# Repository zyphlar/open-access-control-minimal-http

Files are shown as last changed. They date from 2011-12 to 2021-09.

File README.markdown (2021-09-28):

Open Access Control - HTTP Minimal Edition
======================================
AKA Open Access Control Interlock
---------------------------------

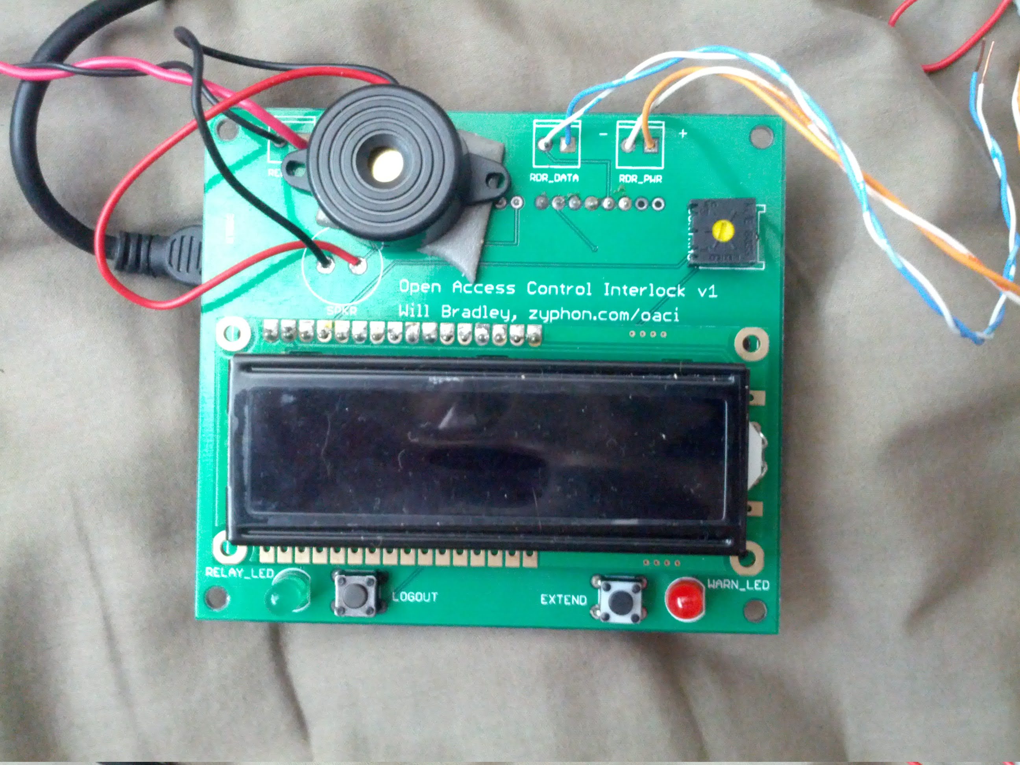
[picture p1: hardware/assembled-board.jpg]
Photo of interlock circuit board
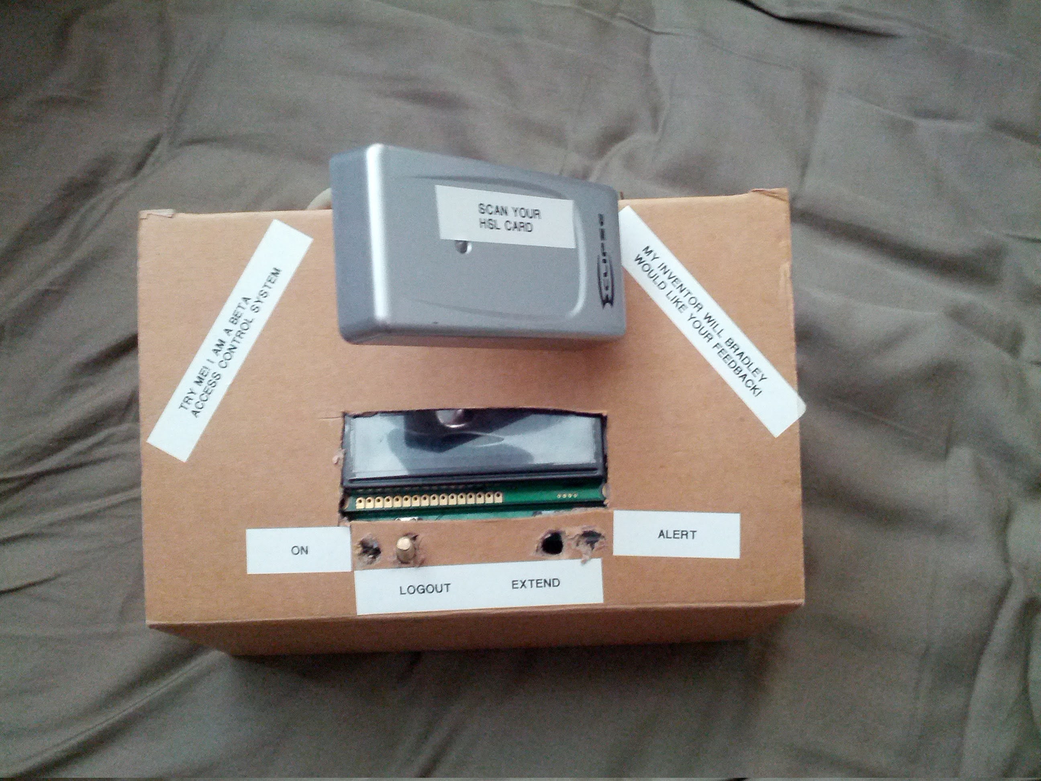
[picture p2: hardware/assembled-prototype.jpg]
Photo of interlock prototype
 

This is a stripped-down version of the 23b hackerspace's Open Access Control system, intended for embedded use with an RFID reader and Ethernet shield for authenticating Wiegand RFID cards with a webservice. Please see http://code.google.com/p/open-access-control/ for the main/full version.

For more info, contact @willbradley on Twitter.

Structure
---------

* This folder
  * Open Access Control folder
    * Open Access Control.ino (Arduino code -- open from the Arduino IDE.)
  * libraries folder (copy the contents of this folder to your Arduino program's libraries folder and restart the Arduino program.)
    * ShiftLCD folder
      * keywords.txt
      * ShiftLCD.cpp
      * ShiftLCD.h
    * PCATTACH folder
      * keywords.txt
      * PCATTACH.cpp
      * PCATTACH.h
    * Wiegand26 folder
      * keywords.txt
      * WIEGAND26.cpp
      * WIEGAND26.h
  * hardware folder
    * open-access-interlock.brd

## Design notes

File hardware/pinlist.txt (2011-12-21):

Pinlist

Exported from open-access-interlock.brd at 12/7/11 2:34 AM

EAGLE Version 5.11.0 Copyright (c) 1988-2010 CadSoft

Part     Pad      Net

ARDUINO  3.3V              *** unconnected ***
         5V       VCC
         A0                *** unconnected ***
         A1                *** unconnected ***
         A2                *** unconnected ***
         A3                *** unconnected ***
         A4       N$14
         A5       N$15
         AREF              *** unconnected ***
         D10               *** unconnected ***
         D11               *** unconnected ***
         D12               *** unconnected ***
         D13               *** unconnected ***
         D2       N$1
         D3       N$2
         D4       N$5
         D5       N$7
         D6       N$6
         D7       N$8
         D8       N$10
         D9       N$9
         GND@0    GND
         GND@1             *** unconnected ***
         GND@2             *** unconnected ***
         RES               *** unconnected ***
         RX                *** unconnected ***
         TX                *** unconnected ***
         VIN               *** unconnected ***

CONTRAST A        VCC
         E        GND
         S        N$18

EXTEND   1                 *** unconnected ***
         2        GND
         3                 *** unconnected ***
         4        N$15

LCD      1        GND
         10                *** unconnected ***
         11       N$12
         12       N$4
         13       N$3
         14       N$20
         15       VCC
         16       N$19
         2        VCC
         3        N$18
         4        N$17
         5        GND
         6                 *** unconnected ***
         7                 *** unconnected ***
         8                 *** unconnected ***
         9                 *** unconnected ***

LOGOUT   1                 *** unconnected ***
         2        GND
         3                 *** unconnected ***
         4        N$14

R1       P$1      N$19
         P$2      GND

R2       P$1      GND
         P$2      N$23

R3       P$1      GND
         P$2      N$22

RDR_DATA 1        N$1
         2        N$2

RDR_PWR  1        VCC
         2        GND

RELAY    1        N$8
         2        GND

RELAY_LED A        N$8
         K        N$23

SHIFT    1        N$3
         10       VCC
         11       N$7
         12       N$6
         13       GND
         14       N$5
         15       N$20
         16       VCC
         2        N$4
         3        N$12
         4                 *** unconnected ***
         5                 *** unconnected ***
         6        N$16
         7        N$17
         8        GND
         9                 *** unconnected ***

SPKR     P$1      N$10
         P$2      GND

WARN_LED A        N$9
         K        N$22

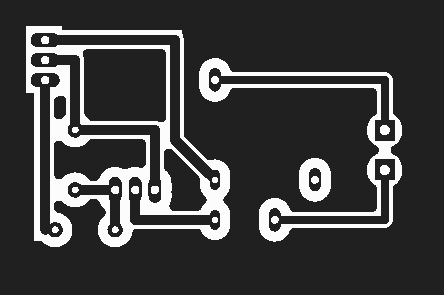
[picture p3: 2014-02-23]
hardware/open-access-interlock-v1-1-relay-5mm.bmp

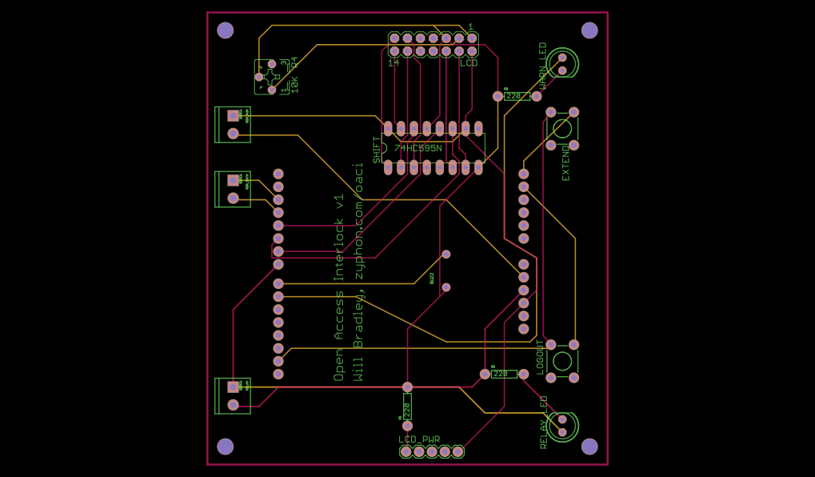
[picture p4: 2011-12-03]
hardware/LASER/full.png

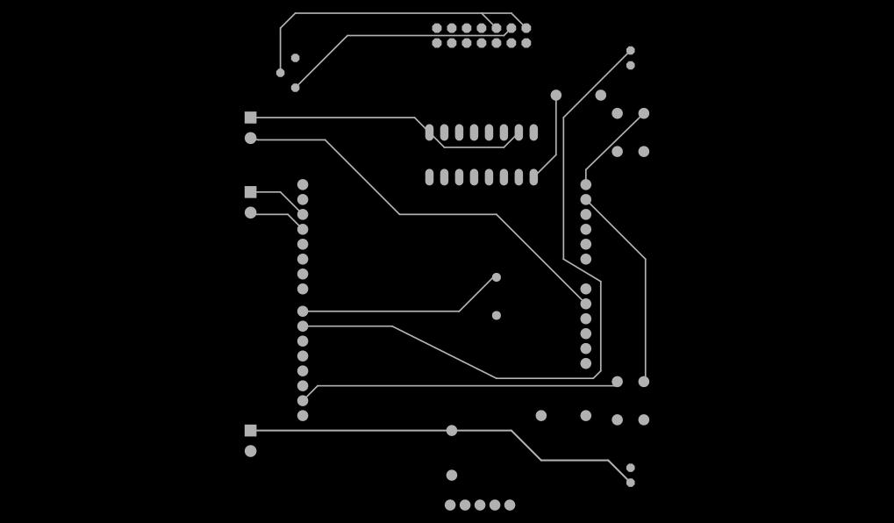
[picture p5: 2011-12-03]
hardware/LASER/bottom.png

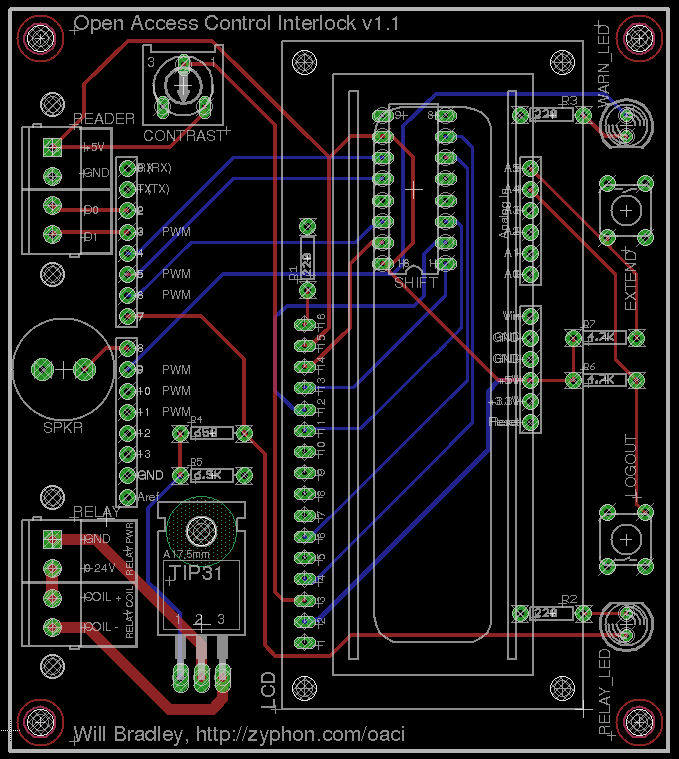
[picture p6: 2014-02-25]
hardware/board.png

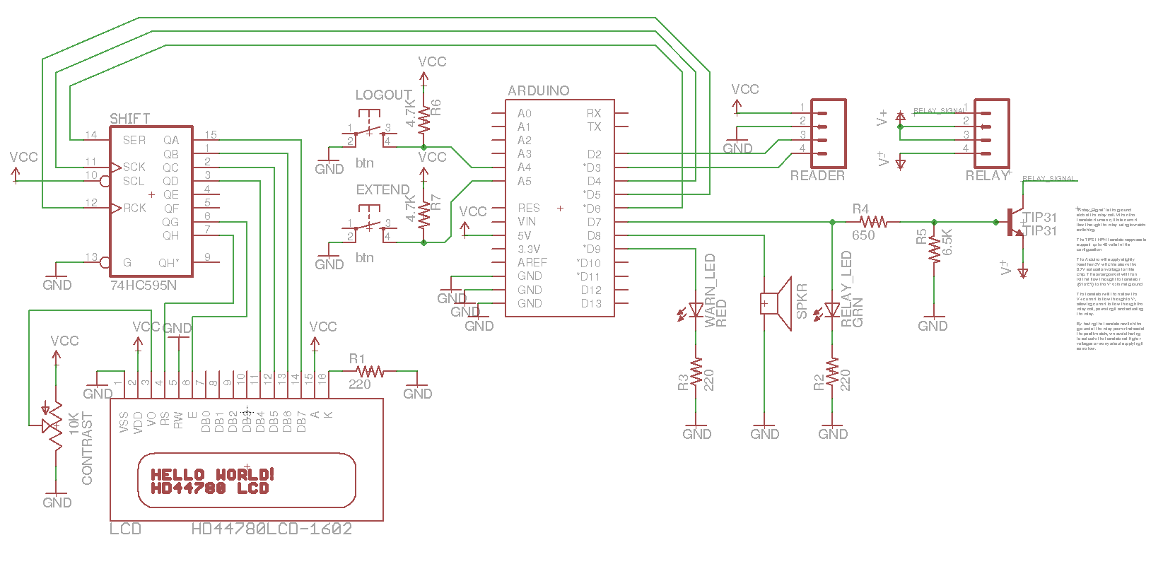
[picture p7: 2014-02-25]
hardware/schematic.png

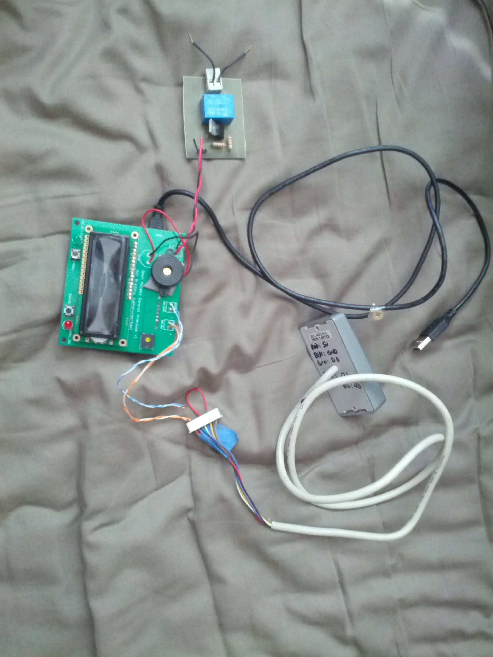
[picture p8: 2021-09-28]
hardware/prototype-guts.jpg

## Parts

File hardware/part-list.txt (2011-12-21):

Partlist

Part      Value                 Device                Package               Library  Sheet

ARDUINO
Shield Headers                  Headers               1x6
Shield Headers                  Headers               1x6
Shield Headers                  Headers               1x8
Shield Headers                  Headers               1x8
SHIFT     74HC595N              Shift Reg             DIL16                 74xx-eu  1
SPKR      SPEAKER/PS12          SPEAKER/PS12          PS12                  adafruit 1
EXTEND    B3F-1060              Button                TACTILE-PTH           SparkFun 1
LOGOUT    B3F-1060              Button                TACTILE-PTH           SparkFun 1
LCD_HDR   1x16                  Header                1x16                  
LCD       HD44780LCD-1602       HD44780LCD-1602       LCD1602               adafruit 1
R1        220ohm                Resistor              AXIAL-0.3             SparkFun 1
R2        220ohm                Resistor              AXIAL-0.3             SparkFun 1
R3        220ohm                Resistor              AXIAL-0.3             SparkFun 1
CONTRAST  10K                   Trim Pot              5x5mm RS3             pot      1
RDR_DATA  SCREW                 Screw Term            SCREWTERMINAL-3.5MM-2 SparkFun 1
RDR_PWR   SCREW                 Screw Term            SCREWTERMINAL-3.5MM-2 SparkFun 1
RELAY     SCREW                 Screw Term            SCREWTERMINAL-3.5MM-2 SparkFun 1
RELAY_LED GRN                   LED 5MM               LED5MM                led      1
WARN_LED  RED                   LED 5MM               LED5MM                led      1

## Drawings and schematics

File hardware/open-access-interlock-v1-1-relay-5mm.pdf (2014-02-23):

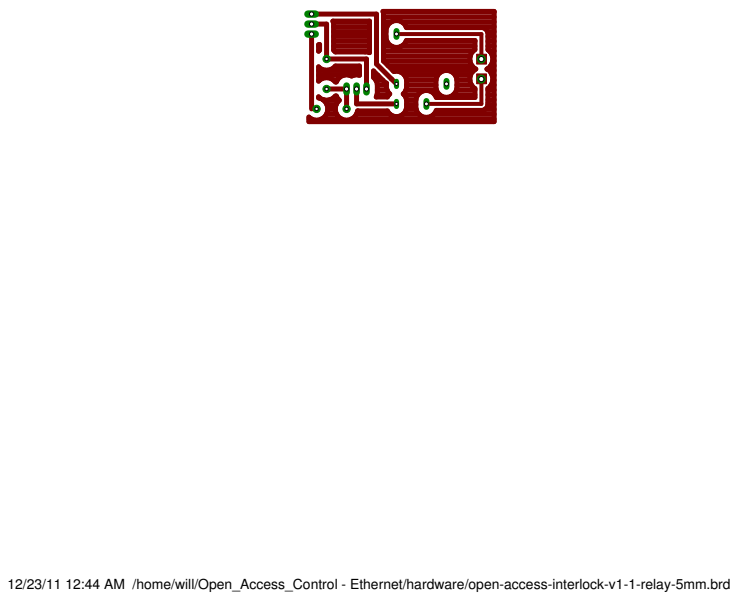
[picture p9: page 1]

12/23/11 12:44 AM /home/will/Open_Access_Control - Ethernet/hardware/open-access-interlock-v1-1-relay-5mm.brd

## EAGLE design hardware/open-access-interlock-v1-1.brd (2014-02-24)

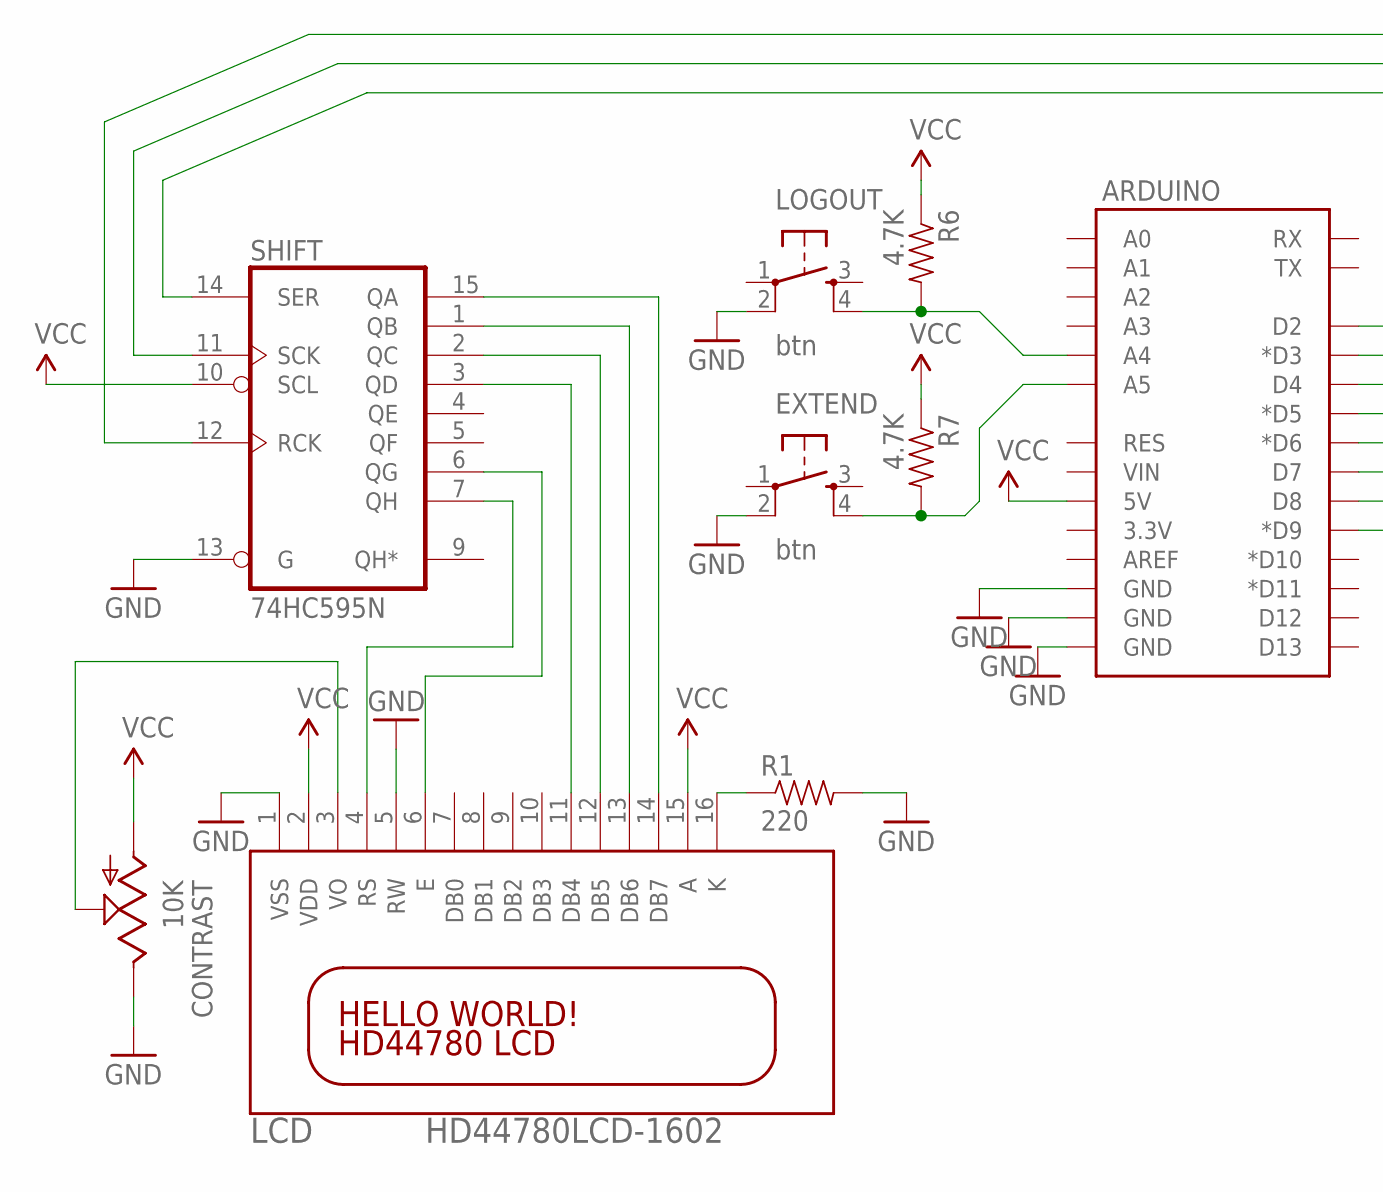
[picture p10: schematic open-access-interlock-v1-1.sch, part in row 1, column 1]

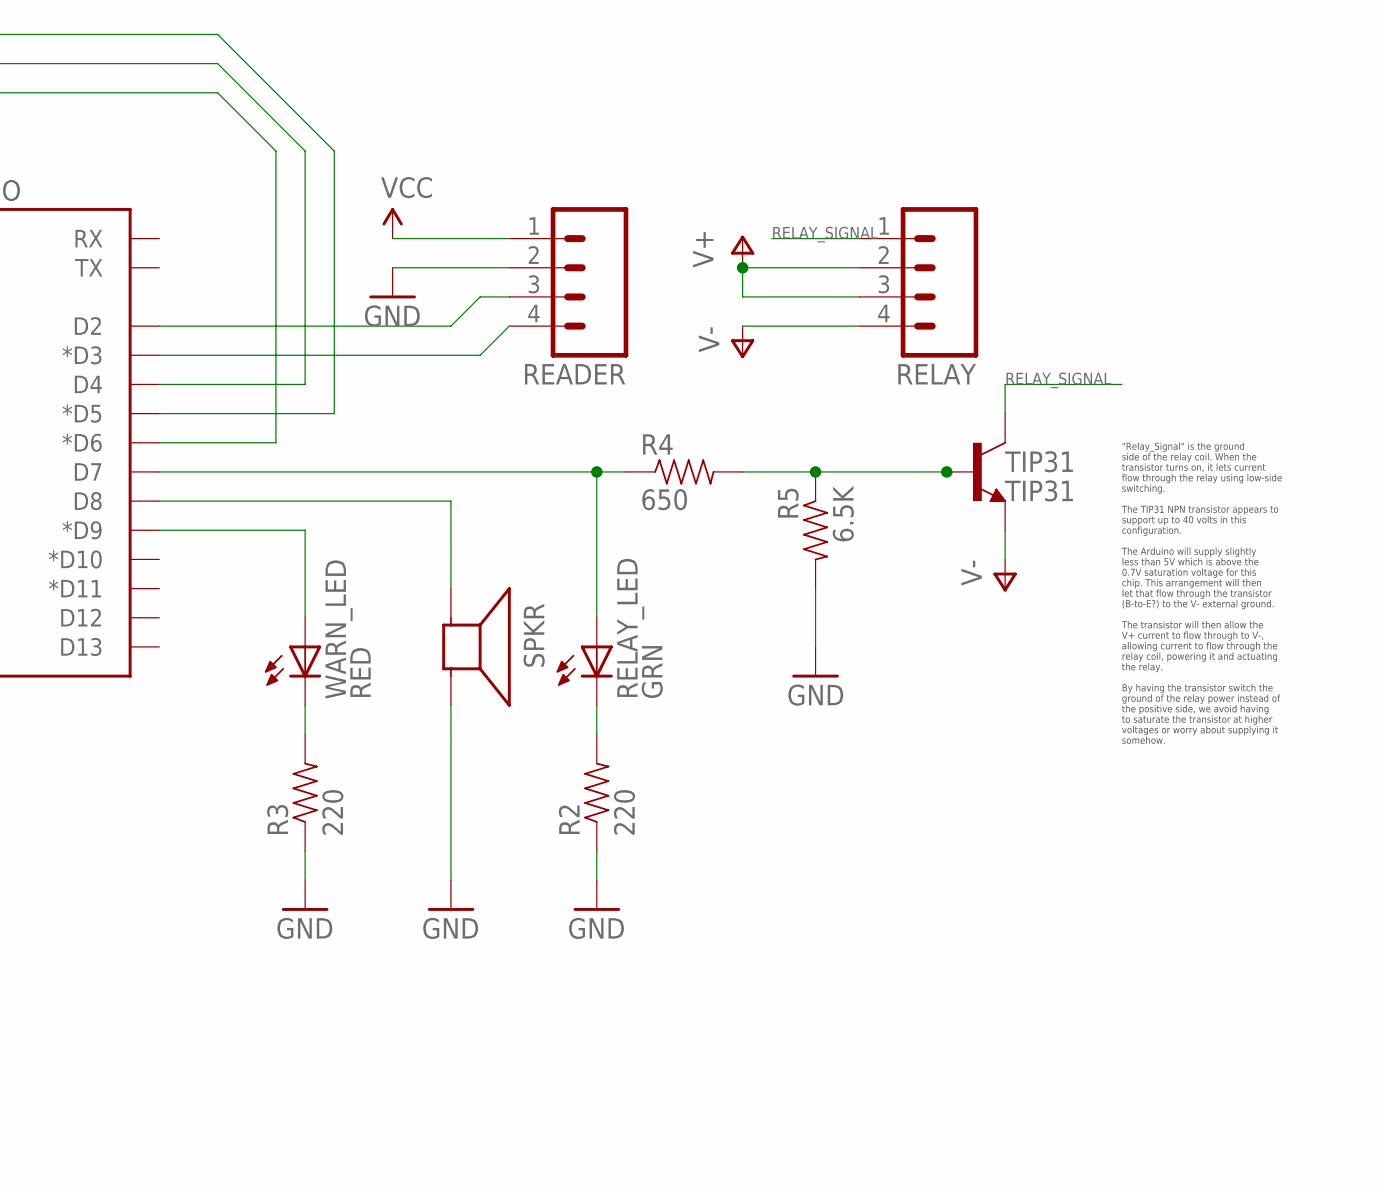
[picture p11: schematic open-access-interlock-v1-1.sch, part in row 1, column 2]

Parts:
ARDUINO: ARDUINO_SHIELDNO_SILK; DUEMILANOVE_VIAS
CONTRAST: 10K; RS3
EXTEND: btn; TACTILE-PTH
LCD: HD44780LCD-1602; LCD1602
LOGOUT: btn; TACTILE-PTH
R1, R2, R3: 220; AXIAL-0.3
R4: 650; AXIAL-0.3
R5: 6.5K; AXIAL-0.3
R6, R7: 4.7K; AXIAL-0.3
READER: M04SCREW; SCREWTERMINAL-3.5MM-4
RELAY: M04SCREW; SCREWTERMINAL-3.5MM-4
RELAY_LED: GRN; LED5MM
SHIFT: 74HC595N; DIL16
SPKR: SPEAKER/PS12; PS12
TIP31: TIP31; TO220
WARN_LED: RED; LED5MM

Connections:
GND: ARDUINO.GND@0 (GND), ARDUINO.GND@1 (GND), ARDUINO.GND@2 (GND), CONTRAST.E, EXTEND.2, LCD.1 (VSS), LCD.5 (RW), LOGOUT.2, R1.P$2 (2), R2.P$1 (1), R3.P$1 (1), R5.P$2 (2), READER.2, SHIFT.8 (GND), SHIFT.13 (G), SPKR.P$2 (-)
unnamed: ARDUINO.D2, READER.3
unnamed: ARDUINO.D3 (*D3), READER.4
unnamed: LCD.13 (DB6), SHIFT.1 (QB)
unnamed: LCD.12 (DB5), SHIFT.2 (QC)
unnamed: ARDUINO.D6 (*D6), SHIFT.14 (SER)
unnamed: ARDUINO.D5 (*D5), SHIFT.12 (RCK)
unnamed: ARDUINO.D4, SHIFT.11 (SCK)
unnamed: ARDUINO.D7, R4.P$1 (1), RELAY_LED.A
unnamed: ARDUINO.D9 (*D9), WARN_LED.A
unnamed: ARDUINO.D8, SPKR.P$1 (+)
unnamed: LCD.6 (E), SHIFT.6 (QG)
unnamed: LCD.11 (DB4), SHIFT.3 (QD)
unnamed: ARDUINO.A4, LOGOUT.4, R6.P$2 (2)
unnamed: ARDUINO.A5, EXTEND.4, R7.P$2 (2)
unnamed: R2.P$2 (2), RELAY_LED.K (C)
unnamed: LCD.4 (RS), SHIFT.7 (QH)
unnamed: CONTRAST.S, LCD.3 (VO)
unnamed: LCD.16 (K), R1.P$1 (1)
unnamed: LCD.14 (DB7), SHIFT.15 (QA)
unnamed: R4.P$2 (2), R5.P$1 (1), TIP31.1 (B)
unnamed: R3.P$2 (2), WARN_LED.K (C)
RELAY_SIGNAL: RELAY.1, TIP31.2 (C)
V+: RELAY.2, RELAY.3
V-: RELAY.4, TIP31.3 (E)
VCC: ARDUINO.5V, CONTRAST.A, LCD.2 (VDD), LCD.15 (A), R6.P$1 (1), R7.P$1 (1), READER.1, SHIFT.10 (SCL), SHIFT.16 (VCC)

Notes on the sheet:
"Relay_Signal" is the ground side of the relay coil. When the transistor turns on, it lets current flow through the relay using low-side switching. The TIP31 NPN transistor appears to support up to 40 volts in this configuration. The Arduino will supply slightly less than 5V which is above the 0.7V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

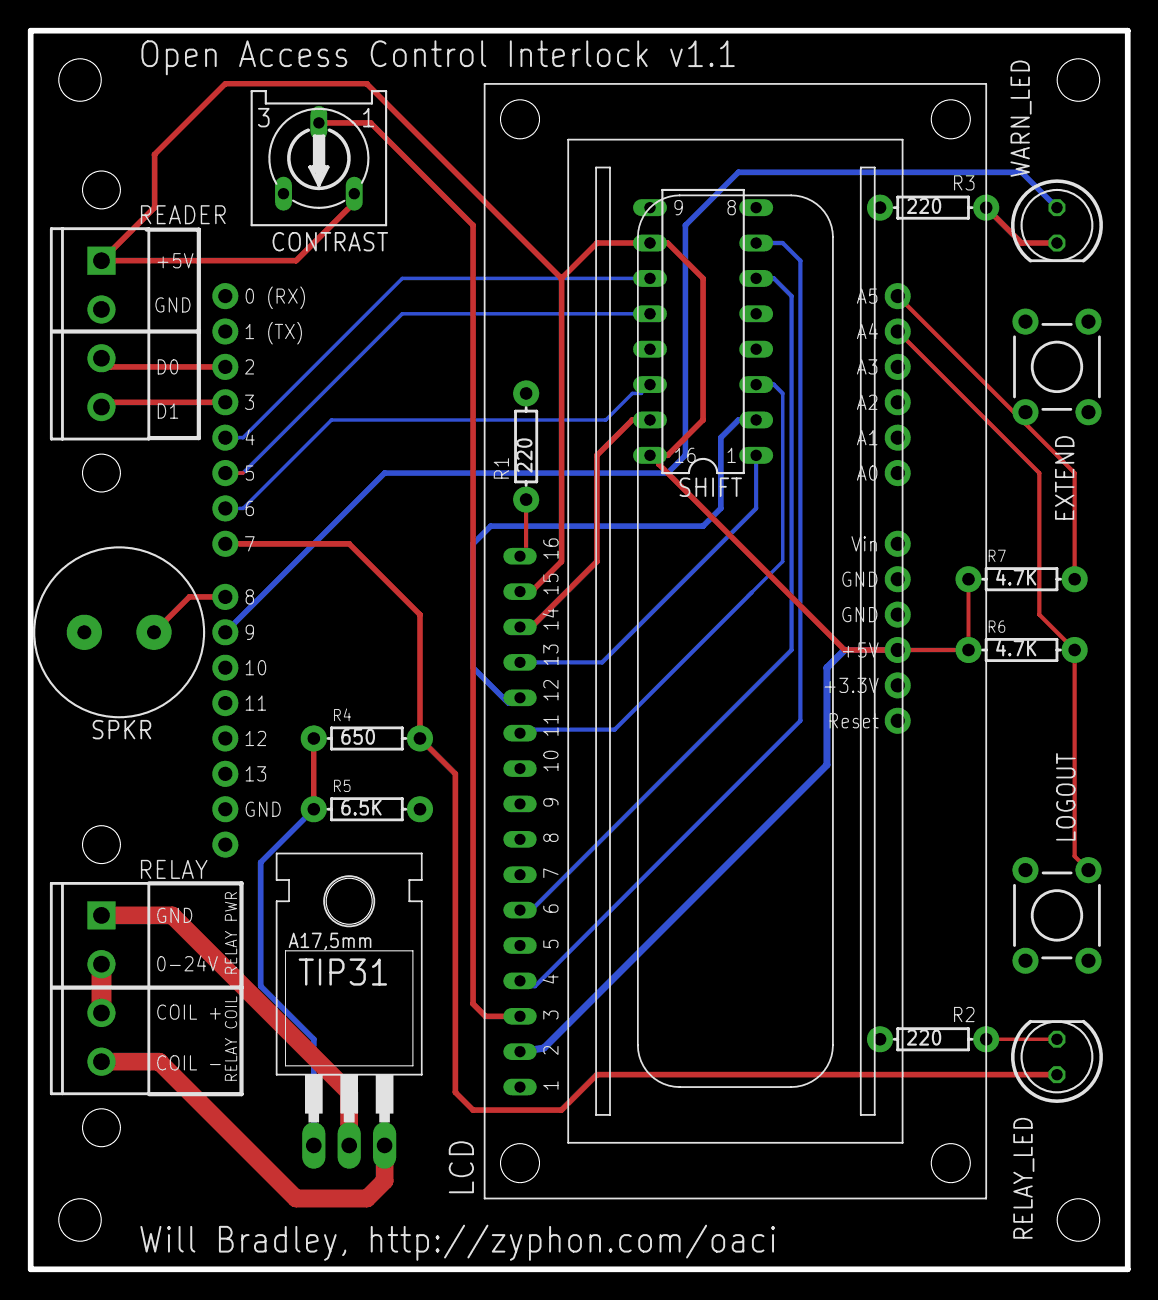
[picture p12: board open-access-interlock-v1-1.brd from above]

Board: 2 copper layers, 78.7 x 88.9 mm, 23 parts (0 on the bottom side), 26 nets.

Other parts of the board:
U$2, U$3, U$4, U$5: STAND-OFF-TIGHT

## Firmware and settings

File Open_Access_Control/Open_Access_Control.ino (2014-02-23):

/*
 * Open Source RFID Access Controller - MINIMAL HTTP EDITION
 * AKA RFID Interlock
 *
 * 02/23/2014 v0.1
 * Last build test with Arduino v1.00
 * 
 * Based on Open Source RFID Access Controller code by:
 * Arclight - arclight@23.org
 * Danozano - danozano@gmail.com
 * See: http://code.google.com/p/open-access-control/
 *
 * Minimal HTTP Edition by:
 * Will Bradley - bradley.will@gmail.com
 * See: https://github.com/zyphlar/open-access-control-minimal-http
 *
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
 * 
 *
 * This program interfaces the Arduino to RFID, PIN pad and all
 * other input devices using the Wiegand-26 Communications
 * Protocol. It is recommended that the keypad inputs be
 * opto-isolated in case a malicious user shorts out the 
 * input device.
 * Outputs go to relays for door hardware/etc control.
 *
 * Relay output on digital pin 7
 * RFID Reader: pins 2,3
 * Ethernet: pins 10,11,12,13 (reserved for the Ethernet shield)
 * LCD: pins 4, 5, 6
 * Warning buzzer: 8
 * Warning LED: 9
 * Extend button: A5
 * Logout button: A4
 *
 * Quickstart tips: 
 * Compile and upload the code, then log in via serial console at 57600,8,N,1
 *
 */
 

/////////////////
// BEGIN USER CONFIGURATION SECTION
/////////////////

// Enter a MAC address, server address, and device identifier for your controller below.
// The IP address will be automatically assigned via DHCP.
char* device = "laser";                       // device identifier (aka "certification slug")
char* server = "members.heatsynclabs.org";    // authorization server (typically Open Access Control Web Interface)
char* user = "YOUREMAILORUSERNAME";        // username to login to server
char* pass = "YOURPASSWORD";                        // password to login to server
byte mac[] = {  0xDE, 0xAD, 0xBE, 0xEF, 0xFE, 0xAD };

/////////////////
// END USER CONFIGURATION SECTION
/////////////////


// Includes
#include <EEPROM.h>       // Needed for saving to non-voilatile memory on the Arduino.

#include <Ethernet.h>
#include <SPI.h>          
#include <Server.h>
#include <Client.h>

#include <WIEGAND26.h>    // Wiegand 26 reader format libary
#include <PCATTACH.h>     // Pcint.h implementation, allows for >2 software interupts.
#include <ShiftLCD.h>     // LCD via shift register

// Create an instance of the various C++ libraries we are using.
WIEGAND26 wiegand26;  // Wiegand26 (RFID reader serial protocol) library
PCATTACH pcattach;    // Software interrupt library

// pin assignments
byte reader1Pins[]={2,3};               // Reader 1 pins
byte RELAYPIN1 = 7;
byte buzzerPin = 8;
byte warningLED = 9;
byte extendButton = A5;
byte logoutButton = A4;

// initialize the ShiftLCD library with the numbers of the interface pins
ShiftLCD lcd(4, 5, 6);

// statics
#define RELAYDELAY 1800000                  // How long to open door lock once access is granted. (1000 = 1sec)

// Serial terminal buffer (needs to be global)
char inString[40]={0};                                         // Size of command buffer (<=128 for Arduino)
byte inCount=0;
boolean privmodeEnabled = false;                               // Switch for enabling "priveleged" commands

// Initialize the Ethernet client library
EthernetClient client;

// strings for storing results from web server
String httpresponse = "";
String username = "";

// variables for storing system status
volatile long reader1 = 0;
volatile int  reader1Count = 0;
bool authorized = false;
bool relay1high = false; 
bool relay2high = false;
unsigned long relay1timer=0;
int extendButtonDebounce = 0;


void setup(){           // Runs once at Arduino boot-up

  /* Attach pin change interrupt service routines from the Wiegand RFID readers
   */
  pcattach.PCattachInterrupt(reader1Pins[0], callReader1Zero, CHANGE); 
  pcattach.PCattachInterrupt(reader1Pins[1], callReader1One,  CHANGE);  
  
  //Clear and initialize readers
  wiegand26.initReaderOne(); //Set up Reader 1 and clear buffers.

  // Initialize button input
  pinMode(extendButton, INPUT);
  digitalWrite(extendButton, HIGH);
  pinMode(logoutButton, INPUT);
  digitalWrite(logoutButton, HIGH);
  
  // Initialize led and buzzer
  pinMode(warningLED, OUTPUT);                                                      
  digitalWrite(warningLED, LOW);                  
  pinMode(buzzerPin, OUTPUT);                                                      
  digitalWrite(buzzerPin, LOW);   

  //Initialize output relays
  pinMode(RELAYPIN1, OUTPUT);                                                      
  digitalWrite(RELAYPIN1, LOW);                  // Sets the relay outputs to LOW (relays off)

  Serial.begin(57600);	               	       // Set up Serial output at 8,N,1,57600bps
  
  // set up the LCD's number of rows and columns: 
  lcd.begin(16, 2);
  lcdprint(0,0,"Starting...");
  
  // start the Ethernet connection:
  if (Ethernet.begin(mac) == 0) {
    lcd.clear();
    lcdprint(0,0,"FAIL: No Network");
    lcdprint(0,1,"Chk DHCP, Reboot");
    // no point in carrying on, so do nothing forevermore:
    for(;;)
      ;
  }
  else {
    lcd.clear();
    lcdprint(0,0,"Found IP:");
    
    Serial.println(Ethernet.localIP());
    lcd.setCursor(0, 1);
    lcd.print(Ethernet.localIP());
  }
  // give the Ethernet shield a second to initialize:
  delay(1000);
  
  lcd.clear();

}
void loop()                                     // Main branch, runs over and over again
{ 
  
  //////////////////////////
  // Normal operation section
  //////////////////////////  
  
  // check timer -- if expired, remove authorization
  
  if(authorized && relay1high) {
   
    // Detect logout button push
    if (analogRead(logoutButton) < 50) {  
      Serial.println("logout");
      authorized = false;
    }
    
    // Detect extend button push with debounce/repeat
    if (analogRead(extendButton) < 50) {  
      extendButtonDebounce++;
    } else {
      extendButtonDebounce = 0;
    } 
    if(extendButtonDebounce > 5){
      Serial.println("extend");
      relay1timer += RELAYDELAY; 
      extendButtonDebounce = -15; 
    }
    
    // calculate current time elapsed
    long currentTime = millis() - relay1timer;
    // if time entirely elapsed, deauthorize.
    if(currentTime >= RELAYDELAY) {
      authorized = false;
    }
    
    // calculate for display
    long remaining = (RELAYDELAY - currentTime) / 1000;
    long secRemaining = (RELAYDELAY - currentTime) / 1000 % 60;
    long minRemaining = (RELAYDELAY - currentTime) / 1000 / 60 % 60;
    long hrsRemaining = (RELAYDELAY - currentTime) / 1000 / 60 / 60;

    // display timer & username
    lcd.setCursor(0, 0);    
    lcd.print(username);
    lcd.setCursor(0, 1);
    lcd.print(hrsRemaining);
    lcd.print(":");
    lcd.print(minRemaining);
    lcd.print(":");
    lcd.print(secRemaining);
    lcd.print(" remain    ");
       
    if(remaining == 300) {
      for(int berp=0; berp<3; berp++){
        tone(buzzerPin, 784, 300); 
        delay(300);
        digitalWrite(warningLED, HIGH);
        tone(buzzerPin, 659, 600); 
        lcd.setCursor(15, 1);        
        lcd.print("!");
        delay(1000);
        digitalWrite(warningLED, LOW);        
        lcd.setCursor(15, 1);        
        lcd.print(" ");
      }
    }
    
    if(remaining == 60) {
      for(int berp=0; berp<5; berp++){
        digitalWrite(warningLED, HIGH);
        lcd.setCursor(15, 1);        
        lcd.print("!");
        tone(buzzerPin, 1047, 100); 
        delay(130);
        tone(buzzerPin, 1109, 100); 
        delay(130);
        tone(buzzerPin, 1109, 100); 
        delay(130);
        tone(buzzerPin, 1109, 100); 
        digitalWrite(warningLED, LOW);
        delay(500);
      }
    }
    
    if(remaining == 15) {
      for(int berp=0; berp<4; berp++){
        digitalWrite(warningLED, HIGH);
        tone(buzzerPin, 1661, 800); 
        delay(800);
        digitalWrite(warningLED, LOW);
        delay(200);
      }
    }
  }
  if(!authorized && relay1high) {
    lcd.clear();
    lcdprint(0,0,"Turning off.");
    delay(500);    
    lcd.clear();    
    
    // not authorized -- turn off relay
    relayLow(1);
    wiegand26.initReaderOne();                     // Reset for next tag scan  
  }
  if(authorized && !relay1high) {
    lcd.clear();
    lcdprint(0,0,"Turning on.");
    delay(500);
    lcd.clear();

    // authorized -- turn on relay
    relayHigh(1);
    wiegand26.initReaderOne();                     // Reset for next tag scan  
  }
  if(!authorized && !relay1high) {
    // display login message
    lcd.setCursor(0,0);
    lcd.print("Please login.");
      
    //////////////////////////  
    // Reader input/authentication section  
    //////////////////////////
    if(reader1Count >= 26)
    {                           //  When tag presented to reader1 (No keypad on this reader)
       
       Serial.print("Reader 1: ");
       Serial.println(reader1, HEX);
       lcdprint(0,0,"connecting...");
       delay(150);
    
       // if you get a connection, report back via serial:
       if (client.connect(server, 80))
       {
         lcd.clear();
         lcdprint(0,0,"connected");
         
         Serial.print("GET /cards/authorize/");   
         Serial.print(reader1, HEX);
         Serial.print("?device=");
         Serial.print(device);
         Serial.print("&user=");
         Serial.print(user);
         Serial.print("&pass=");
         Serial.print(pass);
         Serial.println(" HTTP/1.0");
         Serial.print("Host: ");
         Serial.println(server);
         Serial.println();
          
         client.print("GET /cards/authorize/");   
         client.print(reader1, HEX);
         client.print("?device=");
         client.print(device);
         client.print("&user=");
         client.print(user);
         client.print("&pass=");
         client.print(pass);
         client.println(" HTTP/1.0");
         client.print("Host: ");
         client.println(server);
         client.println();
  
         // reset values coming from http
         httpresponse = "";
         username = "";
         authorized = false;
       }
       else 
       {
         // if you didn't get a connection to the server:
         Serial.println("connection failed");
         lcd.clear();
         lcdprint(0,0,"connection failed");
         delay(500);
         lcd.clear();
       }
       
       wiegand26.initReaderOne();                     // Reset for next tag scan  
       
    }
  
    
    while (client.available()) {
      char thisChar = client.read();
      Serial.print(thisChar);
      // only fill up httpresponse with data after a [ sign.
      // limit total text to 50 to prevent buffer issues
      if ((httpresponse.charAt(0) == '[' || thisChar == '[')  && httpresponse.length() < 50) { 
        httpresponse += thisChar;
      }
    }
    
    if(!client.available() && httpresponse.length()>0) { 
      Serial.println("Response: ");
      
      Serial.println(httpresponse);
      int c = httpresponse.indexOf('[');
      int d = httpresponse.indexOf(',');
      int e = httpresponse.indexOf(']');
      
      Serial.print("IndexOf:");
      Serial.println(c);
      Serial.println(d);
      Serial.println(e);
      
      Serial.println("AuthSubStr:");
      Serial.println(httpresponse.substring(c+1,d));
      
      if(httpresponse.substring(c+1,d) == "true") {
        authorized = true; 
      }
      else {
        Serial.println(httpresponse.substring(c+1,d));
      }
      
      Serial.print("Auth: ");
      Serial.println(authorized);
      
      
      Serial.println("UserSubStr:");
      Serial.println(httpresponse.substring(d+1,e));
  
      String username_raw = httpresponse.substring(d+1,e);
      username_raw.replace("\"", "");
      Serial.print("UserTrimmed: ");
      Serial.println(username_raw);
  
      username = username_raw;
      
      Serial.print("User: ");
      Serial.println(username);
      
      
      Serial.println("End Response");
      httpresponse = "";
      
      if(!authorized) {
        lcd.clear();
        lcdprint(0,0,"Not authorized.");
        delay(500);
      }
    }
    
    // if the server's disconnected, stop the client:
    if (!client.connected()) {
      client.stop();
    }
    
  }
  
  
} // End of loop()


void lcdprint(int x, int y, char* text) {
  Serial.println(text);
  // set the cursor to column 0, line 1
  // (note: line 1 is the second row, since counting begins with 0):
  lcd.setCursor(x, y);
  // print the number of seconds since reset:
  lcd.print(text);
}

/* Access System Functions - Modify these as needed for your application. 
 These function control lock/unlock and user lookup.
 */

void relayHigh(int input) {          //Send an unlock signal to the door and flash the Door LED

relay1timer = millis();

byte dp=1;
  if(input == 1) {
    dp=RELAYPIN1; }
    
  digitalWrite(dp, HIGH);
  
  if (input == 1) {
    relay1high = true;
  }
  
  Serial.print("Relay ");
  Serial.print(input,DEC);
  Serial.println(" high");

}

void relayLow(int input) {          //Send an unlock signal to the door and flash the Door LED
byte dp=1;
  if(input == 1) {
    dp=RELAYPIN1; }

  digitalWrite(dp, LOW);

  if (input == 1) {
    relay1high = false;
  }

  Serial.print("Relay ");
  Serial.print(input,DEC);
  Serial.println(" low");

}


/* Wrapper functions for interrupt attachment
 Could be cleaned up in library?
 */
void callReader1Zero(){wiegand26.reader1Zero();}
void callReader1One(){wiegand26.reader1One();}
void callReader2Zero(){wiegand26.reader2Zero();}
void callReader2One(){wiegand26.reader2One();}
void callReader3Zero(){wiegand26.reader3Zero();}
void callReader3One(){wiegand26.reader3One();}

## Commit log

2011-11-28 Got timer working
2011-11-30 Added extend button
2011-11-30 Logout button working
2011-11-30 Adding hardware
    [open-access-interlock.brd, open-access-interlock.sch]
2011-12-03 Made extend button able to extend past 30 minutes
2011-12-03 Revert "Adding hardware"
    This reverts commit f4d6aa5d7036346dabfb8877d4a0cfdd3cbdc8cb.
    [open-access-interlock.brd, open-access-interlock.sch]
2011-12-03 Added alarms (buzzer and led)
    [Open_Access_Control.pde]
2011-12-03 Revert "Revert "Adding hardware""
    This reverts commit c0f7f7396359c05a34af1b3f2b47c57ebe1d9022.
    [open-access-interlock.brd, open-access-interlock.sch]
2011-12-03 Fixed stray lines and comments
    [Open_Access_Control.pde]
2011-12-03 Added more hardware
    [open-access-interlock.brd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]
2011-12-07 More hardware work
    [open-access-interlock-bottom.dxf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]
2011-12-07 Switched to 16x1 lcd header instead of 7x2
    [open-access-interlock.brd, open-access-interlock.sch]
2011-12-07 Routed the new lcd
    [open-access-interlock.brd, open-access-interlock.sch]
2011-12-07 Updated board layout, widths, speaker component
    [open-access-interlock.brd, open-access-interlock.sch]
2011-12-07 Changed pot to 5mm x 5mm footprint
    [open-access-interlock.brd, open-access-interlock.sch]
2011-12-21 Fixing 465-456 pin error, pin6 mishap, adding transistor/resistors, moving lcd lower
    [open-access-interlock-v1-1-relay.brd, open-access-interlock-v1-1-relay.sch, open-access-interlock-v1-1.brd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]
2014-02-23 Readme update, relay files
    [open-access-interlock-v1-1-relay-5mm.brd, open-access-interlock-v1-1-relay-5mm.sch, open-access-interlock-v1-1-relay.brd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]
2014-02-23 Arduino 1.0 compat, minor tweaks, fixing LCD
    [Open_Access_Control.ino]
2014-02-23 Library Arduino 1.0 compatibility
2014-02-23 Added pullup resistors, moved LCD slightly
    [open-access-interlock-v1-1.brd, open-access-interlock-v1-1.sch]
2014-02-23 Updated with better screw terminals
    [open-access-interlock-v1-1.brd, open-access-interlock-v1-1.sch]
2014-02-23 Final tweaks for terminals and labels
    [open-access-interlock-v1-1.brd, open-access-interlock-v1-1.sch]
2014-02-23 Removing old files
    [open-access-interlock-bottom.dxf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]
2014-02-24 Fixing transistor/relay stuff
    [open-access-interlock-v1-1.brd, open-access-interlock-v1-1.sch]
2014-02-24 Ripping up terminal blocks
    [open-access-interlock-v1-1.brd, open-access-interlock-v1-1.sch]
2014-02-24 Mounting holes, routing tweaks
    [open-access-interlock-v1-1.brd, open-access-interlock-v1-1.sch]
2014-02-24 Seedstudio DRU rules
    [open-access-interlock-v1-1.brd]
2014-02-25 Updating board/schematic png

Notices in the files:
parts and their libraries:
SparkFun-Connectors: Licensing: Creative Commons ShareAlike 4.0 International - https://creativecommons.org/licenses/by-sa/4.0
